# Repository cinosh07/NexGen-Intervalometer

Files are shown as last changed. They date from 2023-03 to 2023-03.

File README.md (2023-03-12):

# NexGen Intervalometer

In this repo you will find the PCB for the intervalometer and 3D print files for the case. 

For the firmware please check link below. The firmware is a part of a camera slider project. This firmware has been develop with polymorphism in mind. So it can be used with a variety of hardware, including this standalone intervalometer. This is configured in the JSON config file that the firmware load at boot.

The firmware is availlable HERE https://github.com/cinosh07/ESP32_Camera_Slider

The interface is accessed by connecting to the Intervalometer hotspot over your mobile web browser. 

**Soon to come:**

**Optional OLED Display with rotary nob to be able to do configurations and operations without using the wireless application.**

To follow the project check out my youtube channel https://youtube.com/@carltremblay

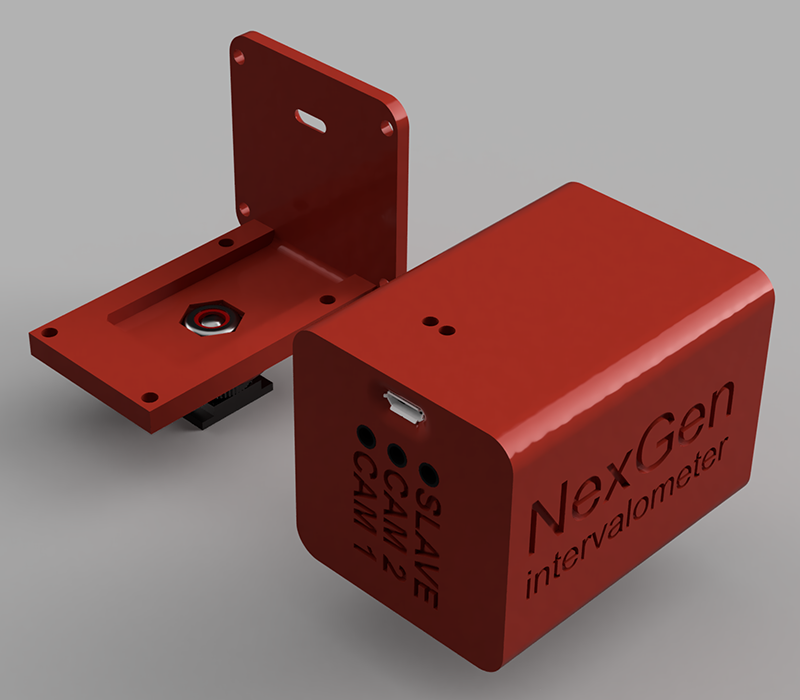
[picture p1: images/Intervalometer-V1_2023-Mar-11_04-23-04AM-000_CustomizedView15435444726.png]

**Here's the intervalometer with the optional flash shoe mount cover.**

# Features
- Easy to use HTML5 interface
- Designed for professionnal timelapse creator
- WIFI hot spot
- Real Time Clock (RTC) 10 ms accuracy over 1 year.
- Holy Grail Ramping
- Precise scheduling start with calendar
- Precise scheduling ramping with calendar
- You can pre-program your session at home and just plug it at location. Thanks to its RTC clock, it will start by itself at the right time. Just leave it and forget.
- Up to 25 shooting profiles that you can manage, rename and configure.
- 0.1 seconds steps
- Bulb Mode
- Easy to follow Interval Timeline display (at the top of the application) that help notice in a snap any conflict in configurations (i.e. Interval shorter than the minimun length require)
- Firmwate update via the web application  
- Camera Sentinel (to keep camera awake)
- Work in cold condition
- Work with Nikon, Canon, Fuji and Sony DSLR Cameras
- Built-in Li-Ion 2100 mAh battery (24 hours autonomy)
- Internal charger (charge in 3 hours @ 1amp)
- Can be powered with power supply for long terme use.
- Dimension: 62mm x 45mm x 45mm
- Dimension: 62mm x 61mm x 45mm (with optional flash hot shoe)
- Weight: < 100g
- And lot more ...

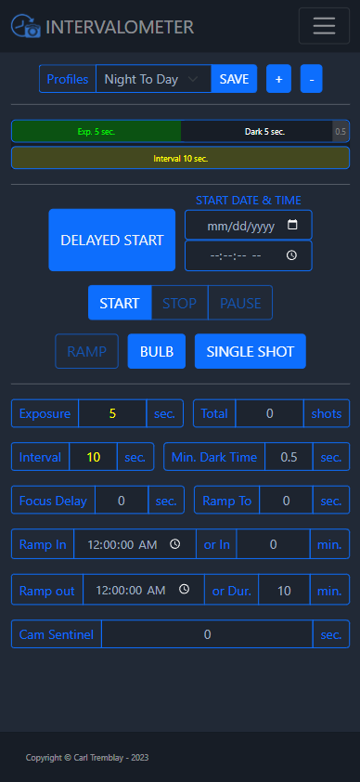
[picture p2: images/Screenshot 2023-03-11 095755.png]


**Web application screenshot**

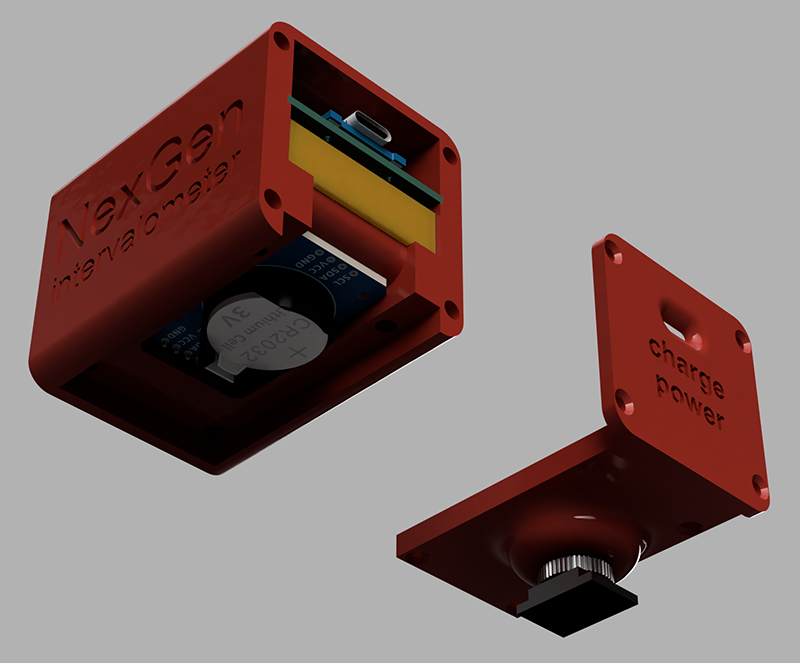
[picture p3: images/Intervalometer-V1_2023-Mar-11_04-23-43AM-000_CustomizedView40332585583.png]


**RTC Clock view**

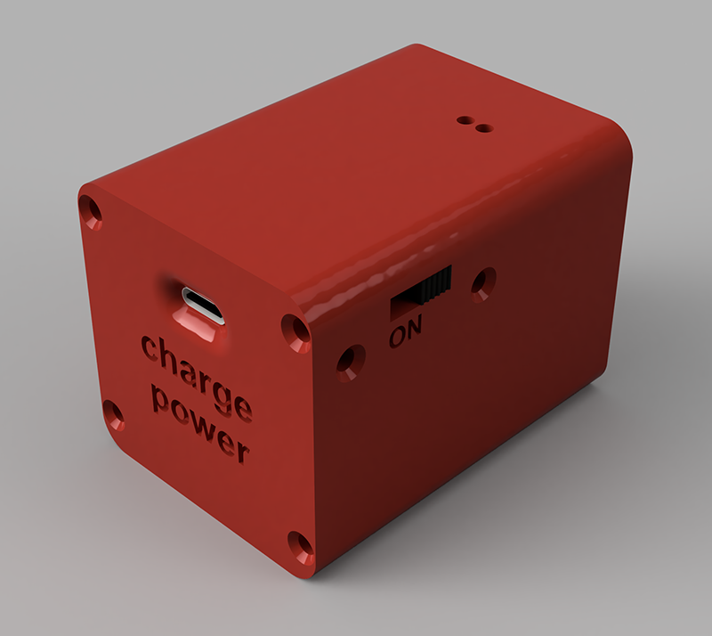
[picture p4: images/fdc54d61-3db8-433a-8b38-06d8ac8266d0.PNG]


**Other side view**

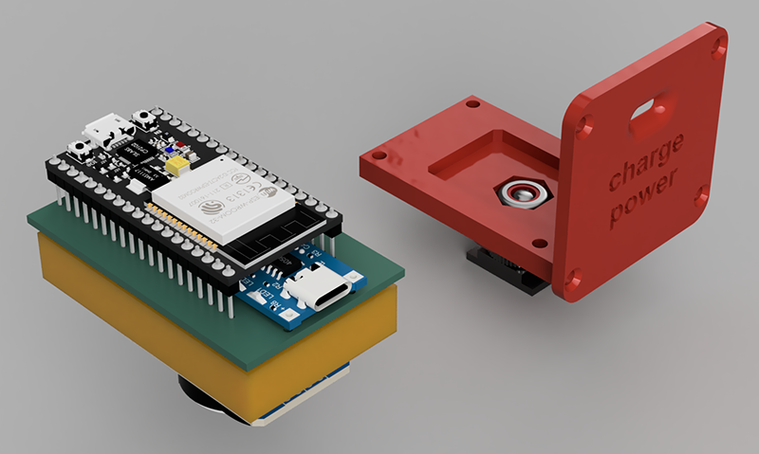
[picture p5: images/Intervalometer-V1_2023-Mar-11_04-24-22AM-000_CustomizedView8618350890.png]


**Inside the intervalometer**

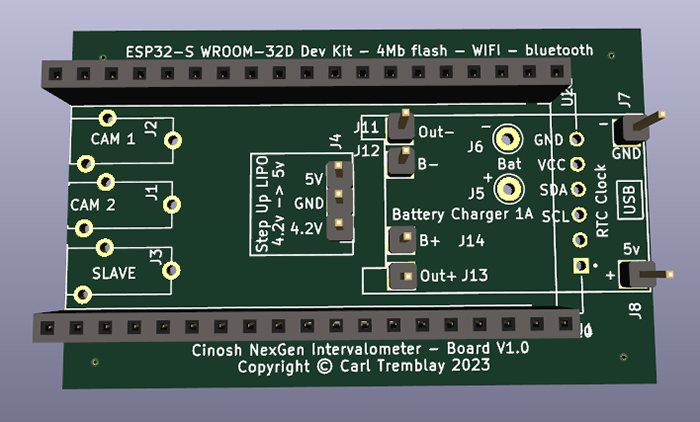
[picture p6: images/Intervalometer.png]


**The PCB**

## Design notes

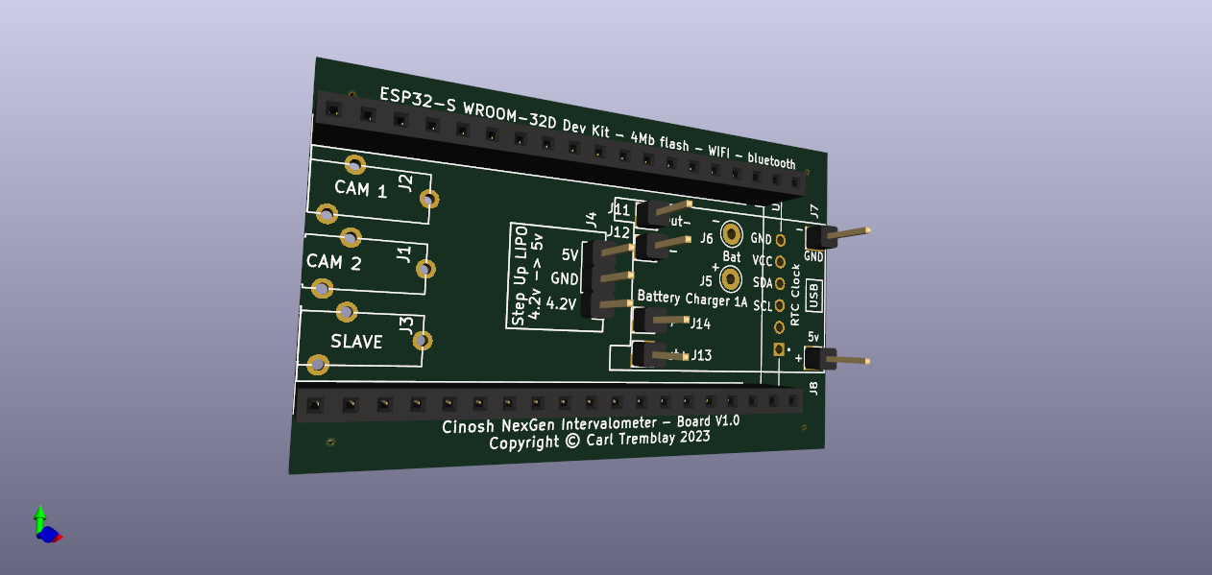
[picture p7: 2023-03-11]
pcb/Intervalometer-2.png

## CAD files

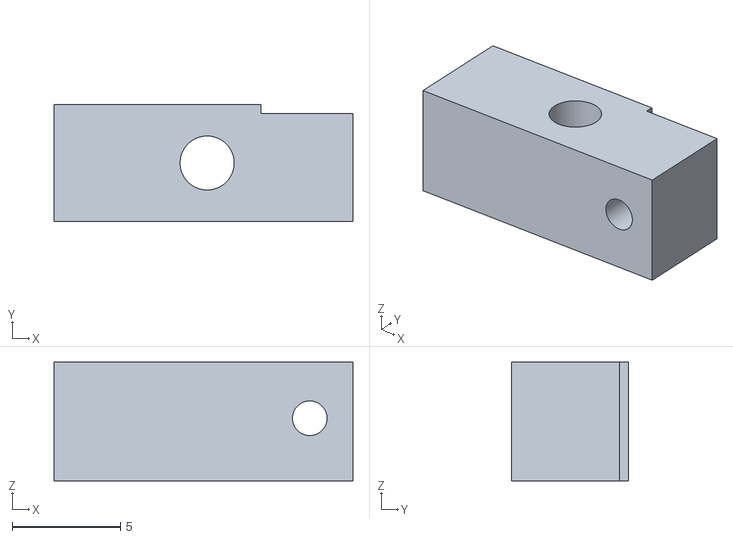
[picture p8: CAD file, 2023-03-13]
3d/Switch holder Right.stl
13.8 x 5.40 x 5.50

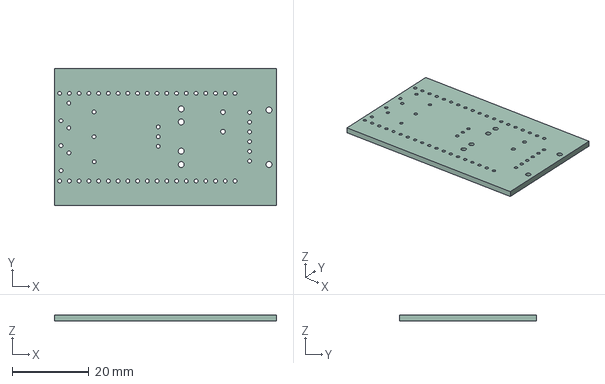
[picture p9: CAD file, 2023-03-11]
pcb/Intervalometer.step
57.9 x 35.7 x 1.58 mm

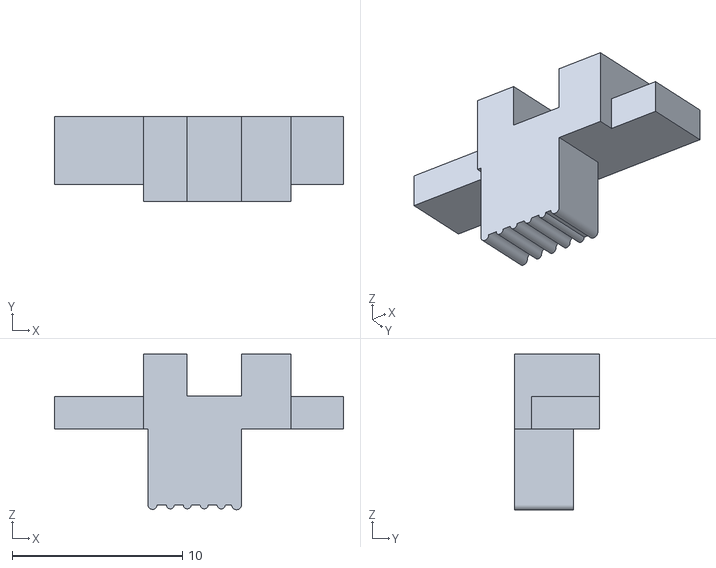
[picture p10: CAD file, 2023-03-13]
3d/Switch.stl
17.0 x 5.00 x 9.15

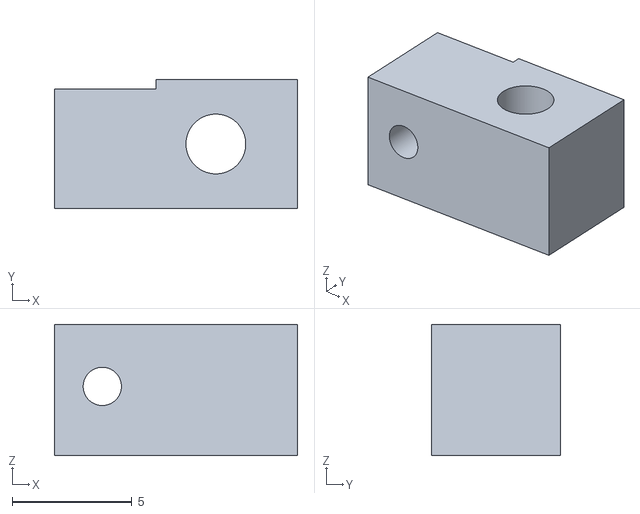
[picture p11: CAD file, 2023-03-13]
3d/Switch holder left.stl
10.2 x 5.40 x 5.50

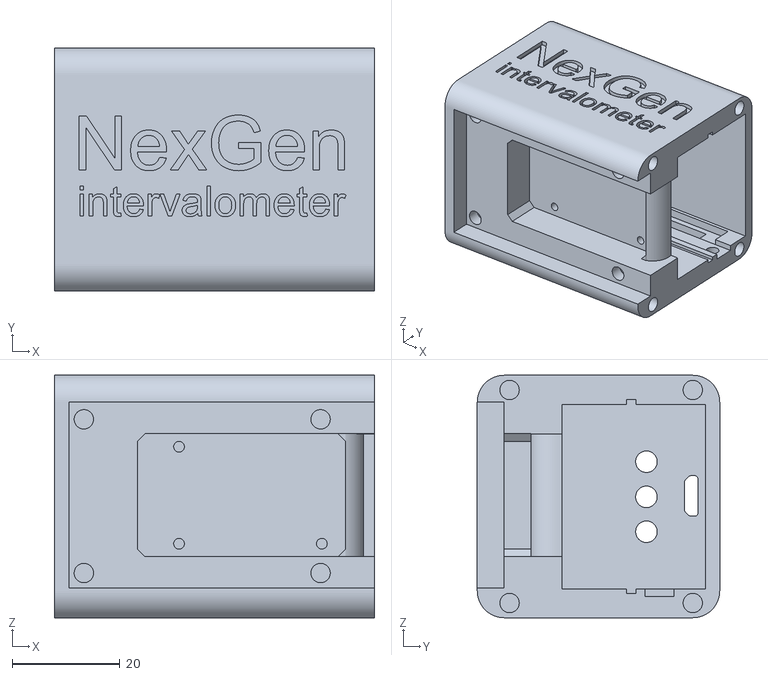
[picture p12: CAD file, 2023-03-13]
3d/Case.stl
59.4 x 45.0 x 45.0

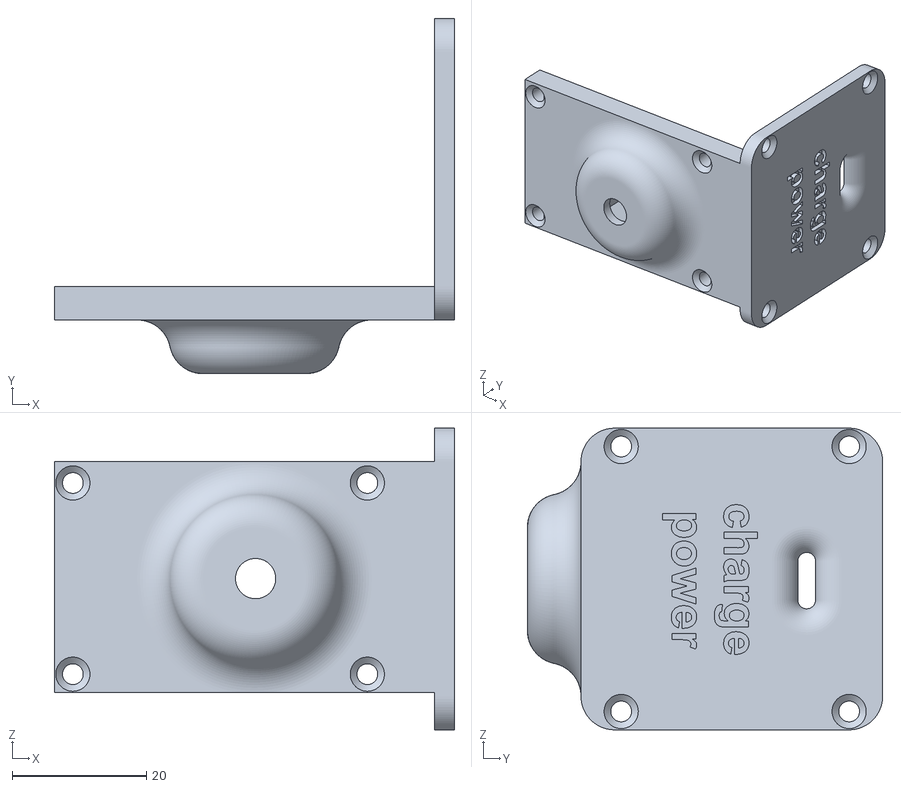
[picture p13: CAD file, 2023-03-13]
3d/cover-hot shoe.stl
59.7 x 53.0 x 45.0

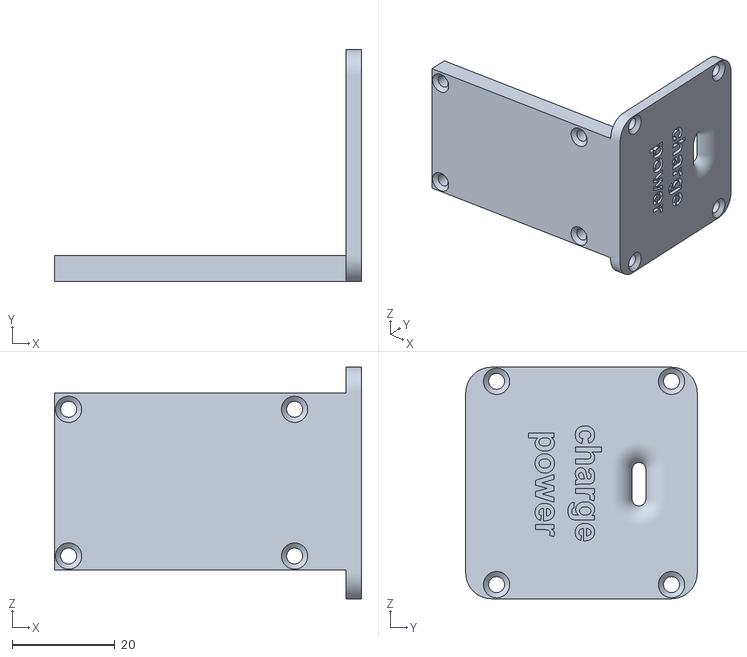
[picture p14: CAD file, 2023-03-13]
3d/cover.stl
59.7 x 45.0 x 45.0

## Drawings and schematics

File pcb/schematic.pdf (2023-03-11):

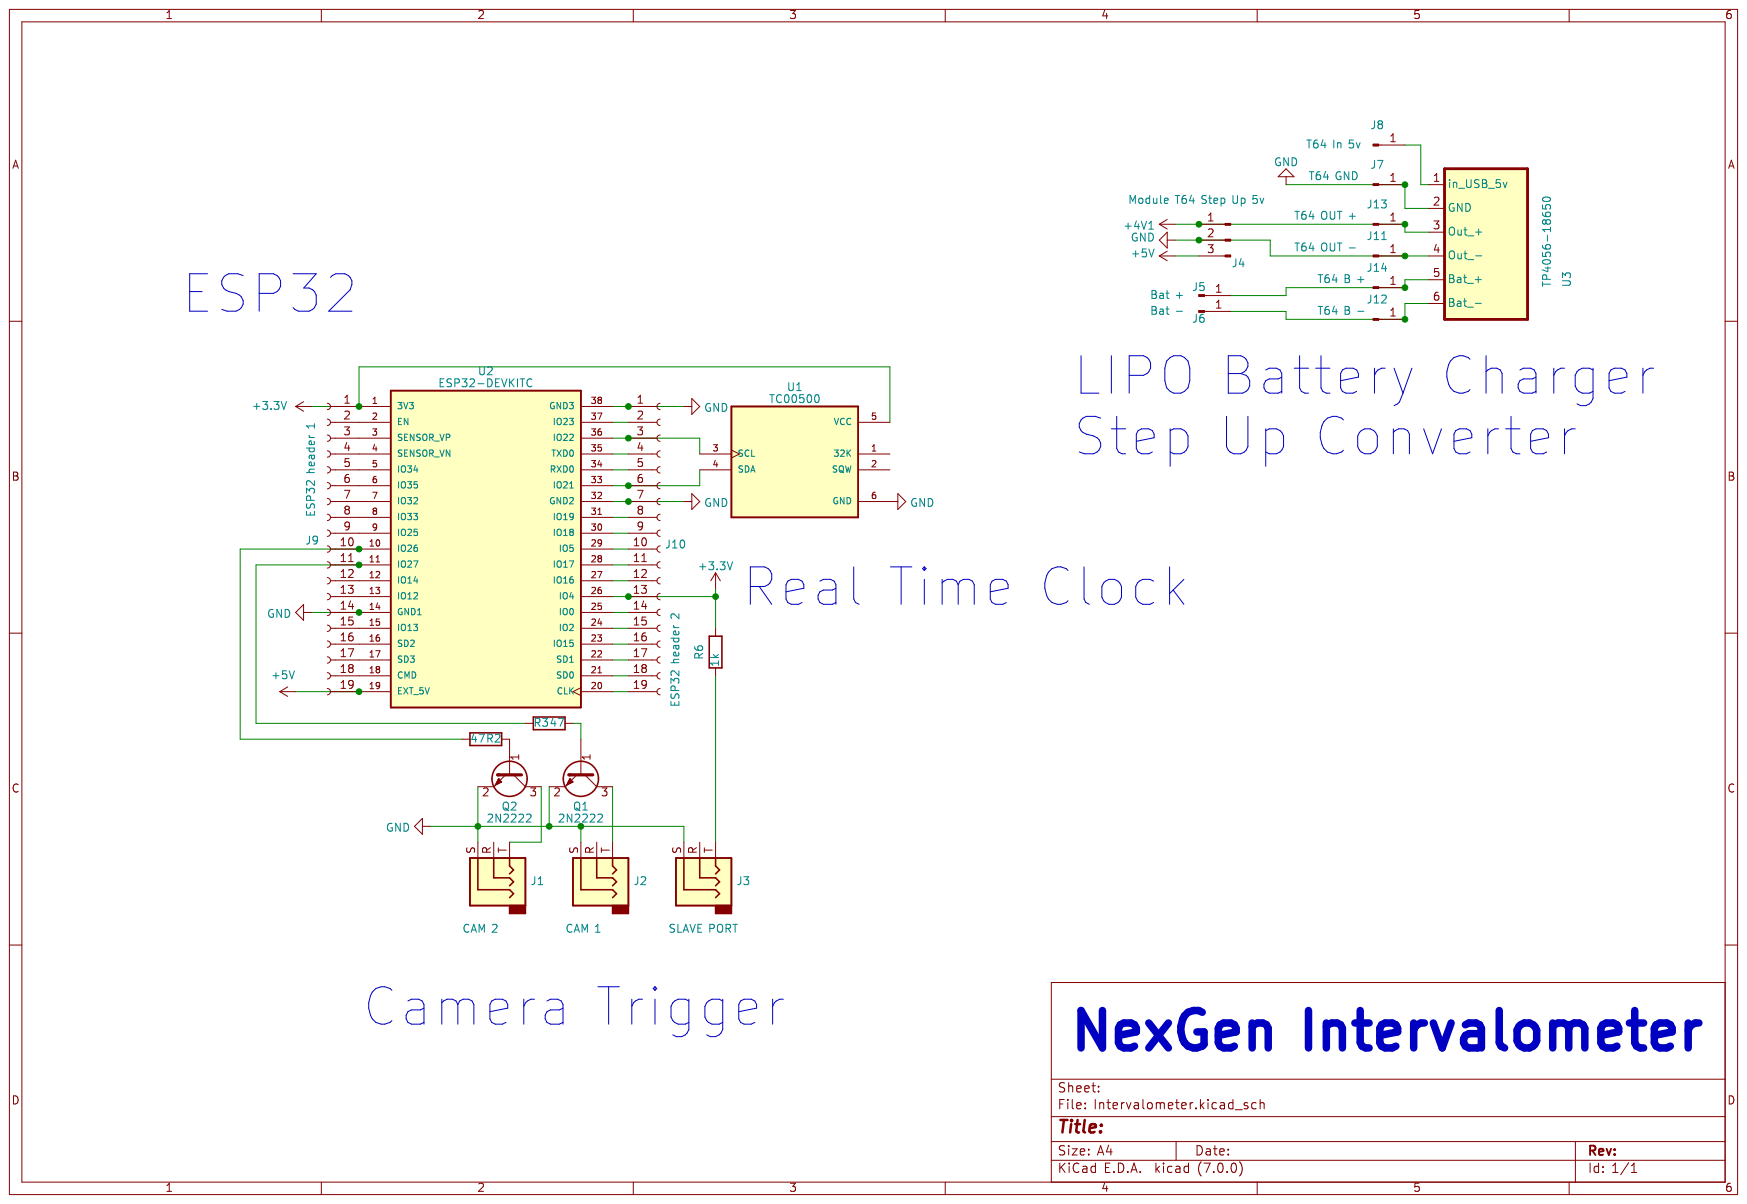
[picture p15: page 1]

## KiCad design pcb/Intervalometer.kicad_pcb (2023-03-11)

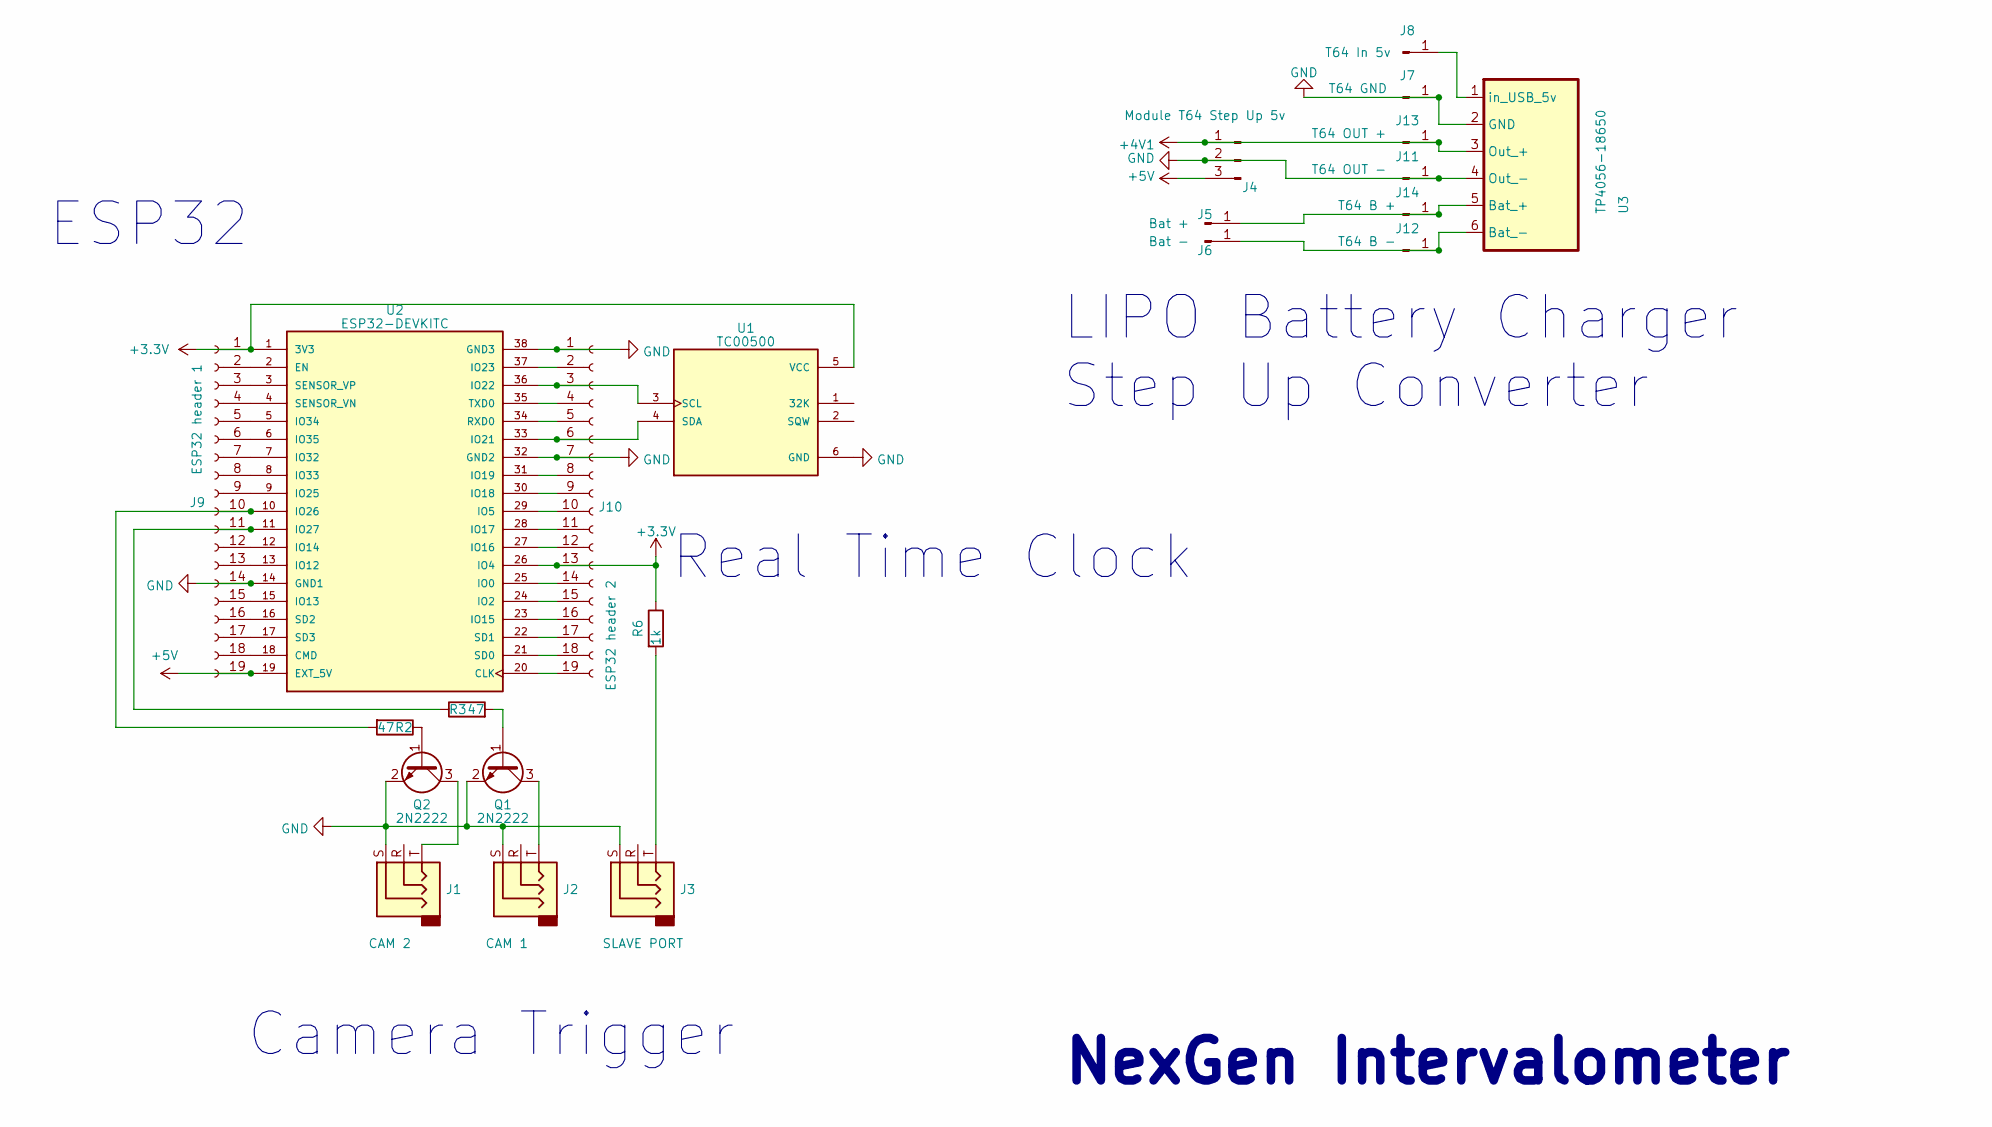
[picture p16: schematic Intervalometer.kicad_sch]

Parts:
J1: CAM 2; Jack_2.5mm_PJ208_Horizontal_CircularHoles
J2: CAM 1; Jack_2.5mm_PJ208_Horizontal_CircularHoles
J3: SLAVE PORT; Jack_2.5mm_PJ208_Horizontal_CircularHoles
J4: Module T64 Step Up 5v; PinHeader_1x03_P2.54mm_Vertical
J5: Bat +; Pin_D1.0mm_L10.0mm_LooseFit
J6: Bat -; Pin_D1.0mm_L10.0mm_LooseFit
J7: T64 GND; PinHeader_1x01_P2.54mm_Vertical
J8: T64 In 5v; PinHeader_1x01_P2.54mm_Vertical
J9: ESP32 header 1; PinSocket_1x19_P2.54mm_Vertical
J10: ESP32 header 2; PinSocket_1x19_P2.54mm_Vertical
J11: T64 OUT -; PinHeader_1x01_P2.54mm_Vertical
J12: T64 B -; PinHeader_1x01_P2.54mm_Vertical
J13: T64 OUT +; PinHeader_1x01_P2.54mm_Vertical
J14: T64 B +; PinHeader_1x01_P2.54mm_Vertical
Q1, Q2: 2N2222; SOT-23
R2, R3: 47; R_0805_2012Metric
R6: 1k; R_0805_2012Metric
U1: TC00500; MODULE_TC00500; PARTREV N/A
U2: ESP32-DEVKITC; MODULE_ESP32-DEVKITC; PARTREV N/A
U3: TP4056-18650

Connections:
+3.3V: J9.1, J10.13, R6.1, U1.5 (VCC), U2.1 (3V3), U2.26 (IO4)
+4V: J4.1, J13.1, U3.3 (Out_+)
+5V: J4.3, J9.19, U2.19 (EXT_5V)
GND: J1.S, J2.S, J3.S, J4.2, J7.1, J9.14, J10.1, J10.7, J11.1, Q1.2 (E), Q2.2 (E), U1.6 (GND), U2.14 (GND1), U2.32 (GND2), U2.38 (GND3), U3.2 (GND), U3.4 (Out_-)
unnamed: J3.T, R6.2
unnamed: J8.1, U3.1 (in_USB_5v)
unnamed: J9.2, U2.2 (EN)
unnamed: J9.3, U2.3 (SENSOR_VP)
unnamed: J9.4, U2.4 (SENSOR_VN)
unnamed: J9.5, U2.5 (IO34)
unnamed: J9.6, U2.6 (IO35)
unnamed: J9.7, U2.7 (IO32)
unnamed: J9.8, U2.8 (IO33)
unnamed: J9.9, U2.9 (IO25)
unnamed: J9.10, R2.2, U2.10 (IO26)
unnamed: J9.11, R3.1, U2.11 (IO27)
unnamed: J9.12, U2.12 (IO14)
unnamed: J9.13, U2.13 (IO12)
unnamed: J9.15, U2.15 (IO13)
unnamed: J9.16, U2.16 (SD2)
unnamed: J9.17, U2.17 (SD3)
unnamed: J9.18, U2.18 (CMD)
unnamed: J10.2, U2.37 (IO23)
unnamed: J10.3, U1.3 (SCL), U2.36 (IO22)
unnamed: J10.4, U2.35 (TXD0)
unnamed: J10.5, U2.34 (RXD0)
unnamed: J10.6, U1.4 (SDA), U2.33 (IO21)
unnamed: J10.8, U2.31 (IO19)
unnamed: J10.9, U2.30 (IO18)
unnamed: J10.10, U2.29 (IO5)
unnamed: J10.11, U2.28 (IO17)
unnamed: J10.12, U2.27 (IO16)
unnamed: J10.14, U2.25 (IO0)
unnamed: J10.15, U2.24 (IO2)
unnamed: J10.16, U2.23 (IO15)
unnamed: J10.17, U2.22 (SD1)
unnamed: J10.18, U2.21 (SD0)
unnamed: J10.19, U2.20 (CLK)
unnamed: J6.1, J12.1, U3.6 (Bat_-)
unnamed: J5.1, J14.1, U3.5 (Bat_+)
unnamed: Q1.1 (B), R3.2
unnamed: J2.T, Q1.3 (C)
unnamed: Q2.1 (B), R2.1
unnamed: J1.T, Q2.3 (C)

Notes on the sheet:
Camera Trigger
NexGen Intervalometer
Real Time Clock
LIPO Battery Charger Step Up Converter
ESP32

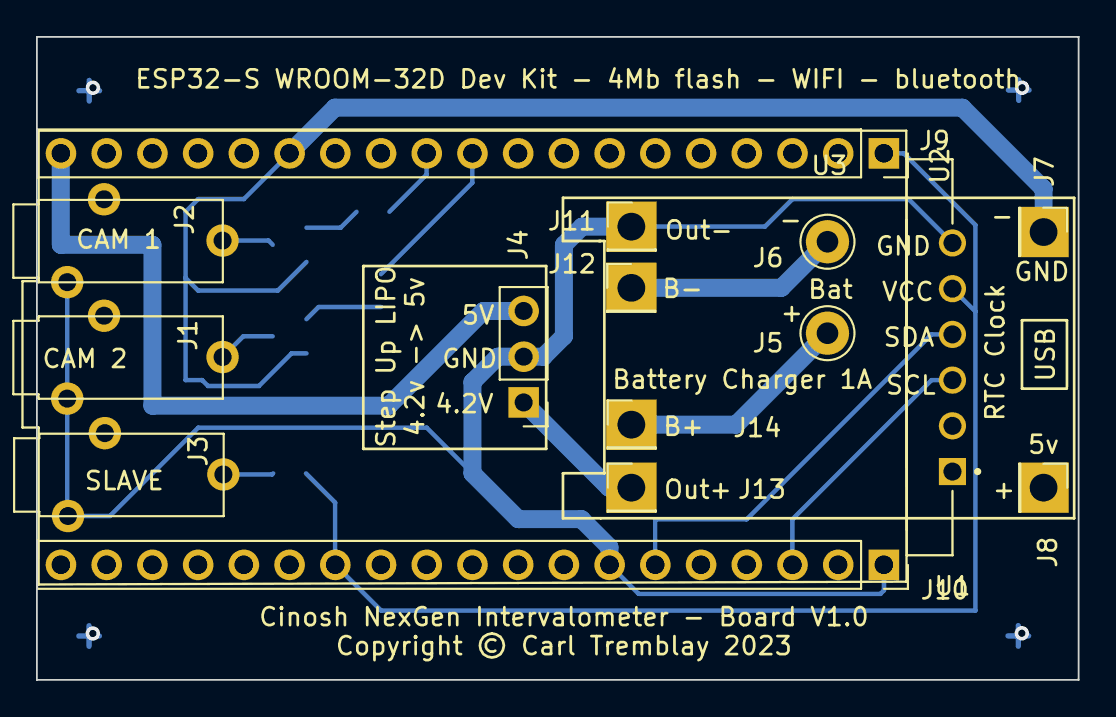
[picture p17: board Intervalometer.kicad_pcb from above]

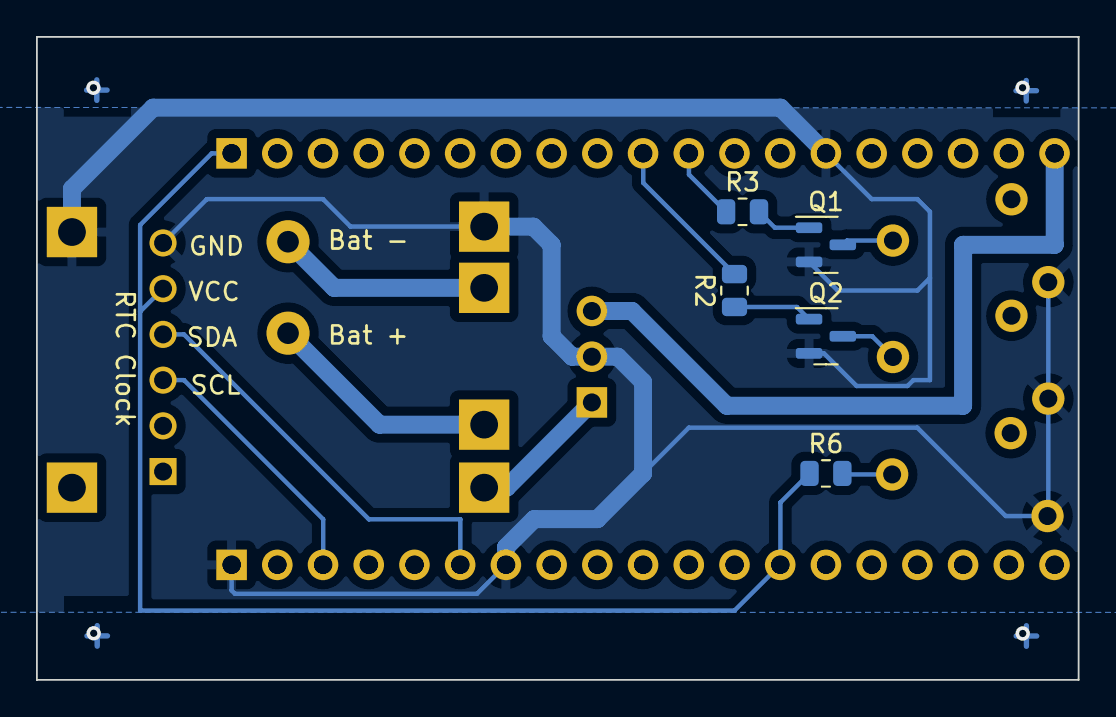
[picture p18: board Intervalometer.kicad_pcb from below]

Board: 2 copper layers, 57.9 x 35.7 mm, 22 parts (5 on the bottom side), 44 nets.

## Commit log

2023-03-12 3d print files
    [Case.stl, Switch holder Right.stl, Switch holder left.stl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]
2023-03-13 Modif grandeurs stl
    [Case.stl, Switch holder Right.stl, Switch holder left.stl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]

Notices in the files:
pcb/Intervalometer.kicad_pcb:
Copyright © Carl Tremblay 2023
